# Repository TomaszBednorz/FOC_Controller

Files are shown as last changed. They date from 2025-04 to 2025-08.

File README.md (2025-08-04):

# FOC_Controller - in progress

## Description

The main goal of this project is to design a driver for a PMSM (Permanent Magnet Synchronous Motor) and implement the FOC (Field-Oriented Control) algorithm in software - in the future.

## Hardware overview



More information: [Hardware folder](https://github.com/TomaszBednorz/FOC_Controller/tree/main/HW)

## Figres

The FOC controller and PMSM motor.  



## STM32CubeIDE template


Empty project with pins and peripherals configuration: [Template](https://github.com/TomaszBednorz/FOC_Controller/tree/main/Tools/STM32CubeIDE_projects/STM32G473RC_template)

## Software overview

TBD

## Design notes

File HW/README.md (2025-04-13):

# FOC_Controller – Hardware

## Description

This folder contains:
- Source files of the PCB design in KiCad: [PCB folder](https://github.com/TomaszBednorz/FOC_Controller/tree/main/HW/PCB)
- STL files for the motor driver enclosure.

## 3D Visualization




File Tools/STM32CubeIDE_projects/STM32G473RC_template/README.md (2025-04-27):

# Configuration overview

## Description

This folder contains an empty project in STM32CubeIDE with the MCU configuration required for further software development. It serves as a project base.



### Clock Configuration
- HSE Value: 24 MHz (Quartz crystal frequency)
- System Clock Frequency: 160 MHz (AHB, APB1, APB2)
- Pins: PF0 [RCC_OSC_IN], PF1: [RCC_OSC_OUT]

### ADC
TODO

### CAN FD
- Baud Rate (Nominal): 1 Mbps
- Baud Rate (Data): 5 Mbps
- Pins: PA11 [CANFD_RX], PA12[CANFD_TX]
  
### SPI - TMAG5170 Hall sensor
- Calculated Baud Rate: 10 Mbps
- SPI mode: 0 (CPOL=0, CPHA=0)
- Data Size: 8-bit
- Direction: 2-line (Full Duplex)
- Pins: PA4 [HALL_SPI_CS], PA5 [HALL_SPI_SCK], PA6: [HALL_SPI_MISO], PA7 [HALL_SPI_MOSI]
  
### UART - Debug
- Baud Rate: 460800 bps
- Pins: PB6 [UART_TX], PB7 [UART_RX]

### Timer - PWM
TODO

### Serial wire debug
- Pins: PA13: [SWD_SWDIO], PA14 [SWD_SWCLK]

### Other GPIO - TODO

// ADC
- PA0: BEMF_C (ADC1_IN1)
- PA1: BEMF_B (ADC1_IN2)
- PA2: BEMF_A (ADC1_IN3)
- PC1: MOTOR_DRV_SOC (ADC1_IN7)
- PC2: MOTOR_DRV_SOB (ADC1_IN8)
- PC3: MOTOR_DRV_SOA (ADC1_IN9)
- PB11: VBAT_SENSE (ADC1_IN14)

// PWM
- PA8: MOTOR_DRV_INHA (TIM1_CH1)
- PA9: MOTOR_DRV_INHB (TIM1_CH2)
- PA10: MOTOR_DRV_INHC (TIM1_CH3)
- PB13: MOTOR_DRV_INLA (TIM1_CH1N)
- PB14: MOTOR_DRV_INLB (TIM1_CH2N)
- PB15: MOTOR_DRV_INLC (TIM1_CH3N)

// GPIO
- PB0: USER_LED - TODO
- PB1: USER_BUTTON - TODO
- PB8: BOOT - TODO
- PC4: HALL_ALERT - Hall sensor interrupt
- PC7: MOTOR_DRV_NFAULT - TODO
- PC8: MOTOR_DRV_NSLEEP - TODO
- PC11: CAN_TRCV_STB - TODO
- PC13: DEBUG_PIN_RED - TODO
- PC15: DEBUG_PIN_BLUE - TODO
- PG10: NRST - TODO

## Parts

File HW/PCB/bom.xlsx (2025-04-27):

Component | Name | Price [zl] | Quantity | Sum | Status | Code case | Link | Designator
Integrated circuits
MCU | STM32G473RCT6 | 20.94 | 2 | 41.88 | Mouser |  | https://www.mouser.pl/ProductDetail/STMicroelectronics/STM32G473RCT6?qs=uwxL4vQweFM8hYulqmXtPg%3D%3D | U2
Motor driver | DRV8317HREER | 9.29 | 2 | 18.58 | Mouser |  | https://www.mouser.pl/ProductDetail/Texas-Instruments/DRV8317HREER?qs=amGC7iS6iy%252BMUwpQq07OLg%3D%3D | U3
CAN-FD transceiver | TCAN3414DR | 5.81 | 2 | 11.62 | Mouser |  | https://www.mouser.pl/ProductDetail/Texas-Instruments/TCAN3413DR?qs=mELouGlnn3eIMT2B6sccyw%3D%3D | U5
Hall sensor | TMAG5170A2QDGKR | 7.1 | 2 | 14.2 | Mouser |  | https://www.mouser.pl/ProductDetail/Texas-Instruments/TMAG5170A2QDGKR?qs=XAiT9M5g4x%2Fpn0mMRKz0SA%3D%3D | U4
Step-down converter | TPS54228D | 4.69 | 2 | 9.38 | Mouser |  | https://www.mouser.pl/ProductDetail/Texas-Instruments/TPS54228D?qs=gXEV9p%2FxLgfhSBr1zrUV%2FQ%3D%3D | U1
Resistors
33k | CRCW080533K0FKEBC | 0.065 | 15 | 0.975 | Mouser | 0805 | https://www.mouser.pl/ProductDetail/Vishay-Dale/CRCW080533K0FKEBC | R1, R5, R21, R23, R25
10k | CRCW080510K0FKEA | 0.172 | 21 | 3.612 | Mouser | 0805 | https://www.mouser.pl/ProductDetail/Vishay-Dale/CRCW080510K0FKEA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 | R2, R4, R7, R10, R22, R24, R26
110k | CRCW0805110KFKEAC | 0.099 | 10 | 0.99 | Mouser | 0805 | https://www.mouser.pl/ProductDetail/Vishay-Dale/CRCW0805110KFKEAC | R3
1k | CRCW08051K00FKEAC | 0.099 | 10 | 0.99 | Mouser | 0805 | https://www.mouser.pl/ProductDetail/Vishay-Dale/CRCW08051K00FKEAC | R6,R8
0R | AC0805FR-070RL | 0.065 | 10 | 0.65 | Mouser | 0805 | https://www.mouser.pl/ProductDetail/YAGEO/AC0805FR-070RL?qs=sGAEpiMZZMvdGkrng054twVr7TWeaA0stZVp9zaHJmE%3D | R9 (brak), R16, R17, R19
5k1 | CRCW08055K10FKEAC | 0.099 | 10 | 0.99 | Mouser | 0805 | https://www.mouser.pl/ProductDetail/Vishay-Dale/CRCW08055K10FKEAC | R11
330R | CRCW0805330RFKEA | 0.103 | 10 | 1.03 | Mouser | 0805 | https://www.mouser.pl/ProductDetail/Vishay-Dale/CRCW0805330RFKEA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 | R12, R13, R14 | -
4k7 | CRCW08054K70FKEA | 0.12 | 10 | 1.2 | Mouser | 0805 | https://www.mouser.pl/ProductDetail/Vishay-Dale/CRCW08054K70FKEA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 | R27
120R | CRCW0805120RFKEA | 0.159 | 10 | 1.59 | Mouser | 0805 | https://www.mouser.pl/ProductDetail/Vishay-Dale/CRCW0805120RFKEA | R28
NC |  |  | 9 | 0 |  |  |  | R15, R19, R20
Capacitors
100u/25V, electrolytic | 860010473007 | 0.53 | 2 | 1.06 | Mouser | THT | https://www.mouser.pl/ProductDetail/Wurth-Elektronik/860010473007 | C1
10u/25V | CL21A106KAYNNNG | 0.301 | 10 | 3.01 | Mouser | 0805 | https://www.mouser.pl/ProductDetail/Samsung-Electro-Mechanics/CL21A106KAYNNNG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 | C2, C3, C11
100n/50V | CL21B104KBCNNND | 0.077 | 100 | 7.7 | Mouser | 0805 | https://www.mouser.pl/ProductDetail/Samsung-Electro-Mechanics/CL21B104KBCNNND?qs=349EhDEZ59q4Uk9cKG1Kkg%3D%3D | C4, C7, C10, C12, C13, C14, C15, C16, C17, C20, C23, C25, C26, C30, C31, C32, C39, C41, C42
1u/50V | CL21B105KBFNNNE | 0.151 | 15 | 2.265 | Mouser | 0805 | https://www.mouser.pl/ProductDetail/Samsung-Electro-Mechanics/CL21B105KBFNNNE?qs=yOVawPpwOwmddQEBPU6Y9A%3D%3D | C5, C18, C19, C24, C40
3n3/25V | 885012207063 | 0.155 | 10 | 1.55 | Mouser | 0805 | https://www.mouser.pl/ProductDetail/Wurth-Elektronik/885012207063?qs=0KOYDY2FL29qg3SFvr%2F81Q%3D%3D | C6
22u/25V | CL21A226MAYNNNE | 0.426 | 15 | 6.39 | Mouser | 0805 | https://www.mouser.pl/ProductDetail/Samsung-Electro-Mechanics/CL21A226MAYNNNE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 | C8, C9, [C27, C28, C29]->22p
27p/50V | CL10C270JB81PNC | 0.116 | 10 | 1.16 | Mouser | 0603 | https://www.mouser.pl/ProductDetail/Samsung-Electro-Mechanics/CL10C270JB81PNC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 | C21, C22
10u/25V, electrolytic | 865080440002 | 0.74 | 4 | 2.96 | Mouser | SMD | https://www.mouser.pl/ProductDetail/Wurth-Elektronik/865080440002 | C33, C35
2u2/25V | CL21A225KAFNNNG | 0.219 | 10 | 2.19 | Mouser | 0805 | https://www.mouser.pl/ProductDetail/Samsung-Electro-Mechanics/CL21A225KAFNNNG?qs=yOVawPpwOwlfuACaawXMWQ%3D%3D | C34
1n6/50V | GRM1885C1H162JA01D | 0.129 | 10 | 1.29 | TME | 0603 | https://www.tme.eu/pl/details/grm1885c1h162ja01d/kondensatory-mlcc-smd/murata/ | C36, C37, C38
47p | CL10C470JC81PNC | 0.163 | 10 | 1.63 | Mouser | 0603 | https://www.mouser.pl/ProductDetail/Samsung-Electro-Mechanics/CL10C470JC81PNC?qs=zijbFIqa2JHu3PDRMJ4hNA%3D%3D | C43, C44
Inductors
3u3 | NRS4012T3R3MDGJ | 0.78 | 3 | 2.34 | Mouser |  | https://www.mouser.pl/ProductDetail/TAIYO-YUDEN/NRS4012T3R3MDGJ?qs=PzICbMaShUd7bwjzDBeuGQ%3D%3D | L1
Diodes
Schottky Diodes | SK22 | 0.74 | 3 | 2.22 | Mouser |  | https://www.mouser.pl/ProductDetail/Diotec-Semiconductor/SK22?qs=OlC7AqGiEDnotPkeKaADTg%3D%3D | D1
LED green | 150080GS75000 | 0.78 | 3 | 2.34 | Mouser |  | https://www.mouser.pl/ProductDetail/Wurth-Elektronik/150080GS75000 | D2
LED blue | 150080BS75000 | 0.78 | 3 | 2.34 | Mouser |  | https://www.mouser.pl/ProductDetail/Wurth-Elektronik/150080BS75000 | D3
Ferrite Beads
600R/100Mhz | MPZ2012S601ATD25 | 0.28 | 10 | 2.8 | Mouser | 0805 | https://www.mouser.pl/ProductDetail/TDK/MPZ2012S601ATD25?qs=n0%2F4YYxsltT7vo9AjVUU7w%3D%3D | FB1
Cristals
24MHz | ABM3-24.000MHZ-D2Y-T | 2.21 | 2 | 4.42 | Mouser |  | https://www.mouser.pl/ProductDetail/ABRACON/ABM3-24.000MHZ-D2Y-T?qs=ihRgKfnEsN7QIYosfWUeVg%3D%3D | X1
Switches
Tactile Switch | TS04-66-55-BK-100-SMT | 0.66 | 4 | 2.64 | Mouser |  | https://www.mouser.pl/ProductDetail/Same-Sky/TS04-66-55-BK-100-SMT | SW1, SW2
Connectors
DC male connector | XT30PW-M | 2.54 | 2 | 5.08 | TME |  | https://www.tme.eu/pl/details/xt30pw-m/zlacza-dc/amass/ | J1
DC female connector | XT30U-F | 1.75 | 2 | 3.5 | TME |  | https://www.tme.eu/pl/details/xt30u-f/zlacza-dc/amass/ | J1
Header 1x10 (goldpin) | 10129378-910001BLF | 0.78 | 2 | 1.56 | Mouser |  | https://www.mouser.pl/ProductDetail/Amphenol-FCI/10129378-910001BLF?qs=0lQeLiL1qyaKTim8PTf2WA%3D%3D | J2, J4
Header 2x5 | 20021121-00010T4LF | 3.23 | 2 | 6.46 | Mouser |  | https://www.mouser.pl/ProductDetail/Amphenol-FCI/20021121-00010T4LF?qs=oJs1R%252BxK6kTva5Su0CuB6g%3D%3D | J3
Screw terminal 1x3 | EBWA-03-A | 1.76 | 2 | 3.52 | Mouser |  | https://www.mouser.pl/ProductDetail/Adam-Tech/EBWA-03-A?qs=HoCaDK9Nz5eL6P8%252BJvt%2FAA%3D%3D | J6
Jumper 1x2 | MSA-G | 0.41 | 3 | 1.23 | Mouser |  | https://www.mouser.pl/ProductDetail/Adam-Tech/MSA-G?qs=TTVbHWoAP%2FQyJO4lrxmkwg%3D%3D | J5
 |  |  | Łącznie | 179.342

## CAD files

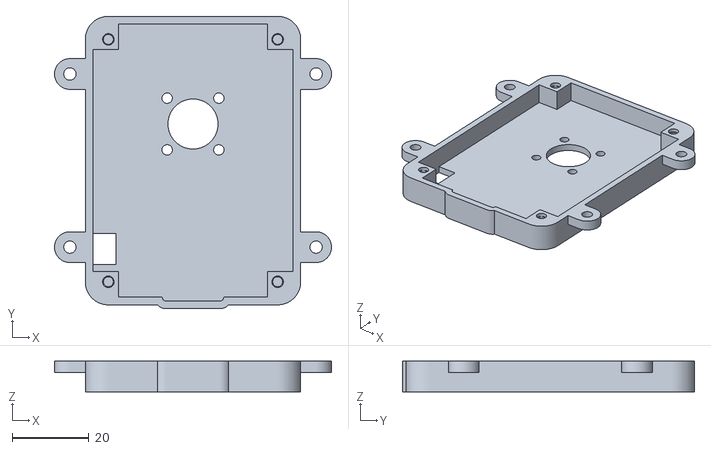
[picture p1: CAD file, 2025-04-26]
HW/Enclosure/Base.stl
72.0 x 76.0 x 8.00

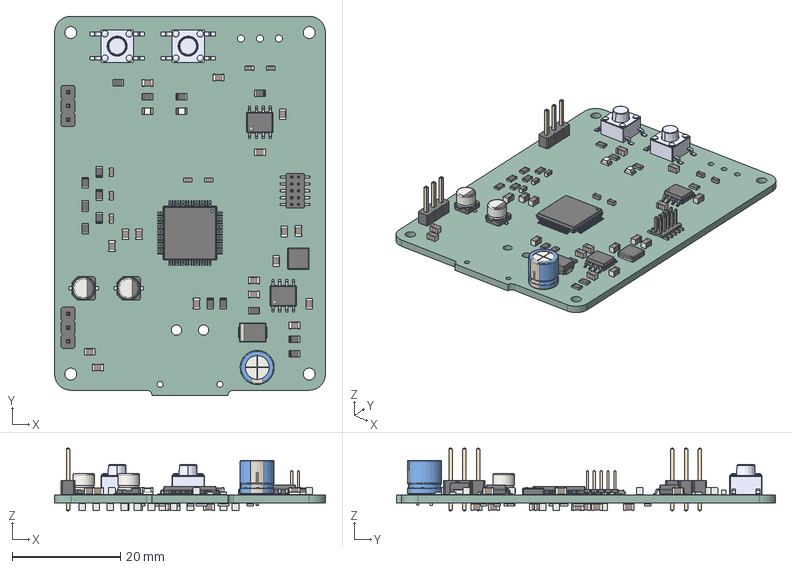
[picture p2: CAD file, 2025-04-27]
HW/PCB/FOC_Controller.step
50.0 x 70.0 x 11.5 mm
C_0805_2012Metric x 34
SOIC-8_3.9x4.9mm_P1.27mm x 2
R_0805_2012Metric x 27
CP_Elec_4x3.9 x 2
C_0603_1608Metric x 7
LQFP-64_10x10mm_P0.5mm
D_SMB
TS04-66-55-BK-100-SMT-TR x 2
L_0805_2012Metric
CP_Radial_D6.3mm_P2.50mm
LED_0805_2012Metric x 2
PinHeader_2x05_P1.27mm_Vertical_SMD
PinHeader_1x03_P2.54mm_Vertical x 2
L_APV_ANR4012
FOC_Controller_PCB

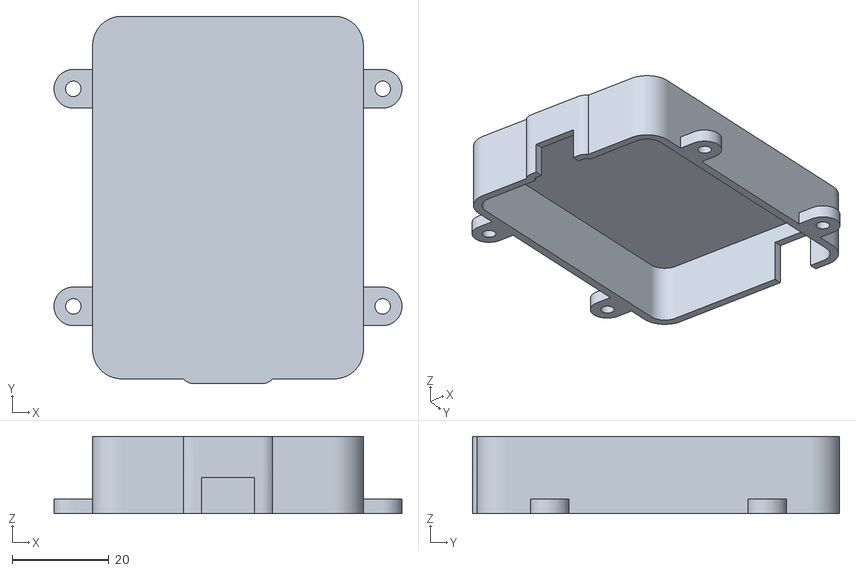
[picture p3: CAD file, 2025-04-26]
HW/Enclosure/Lid.stl
72.0 x 76.0 x 16.0

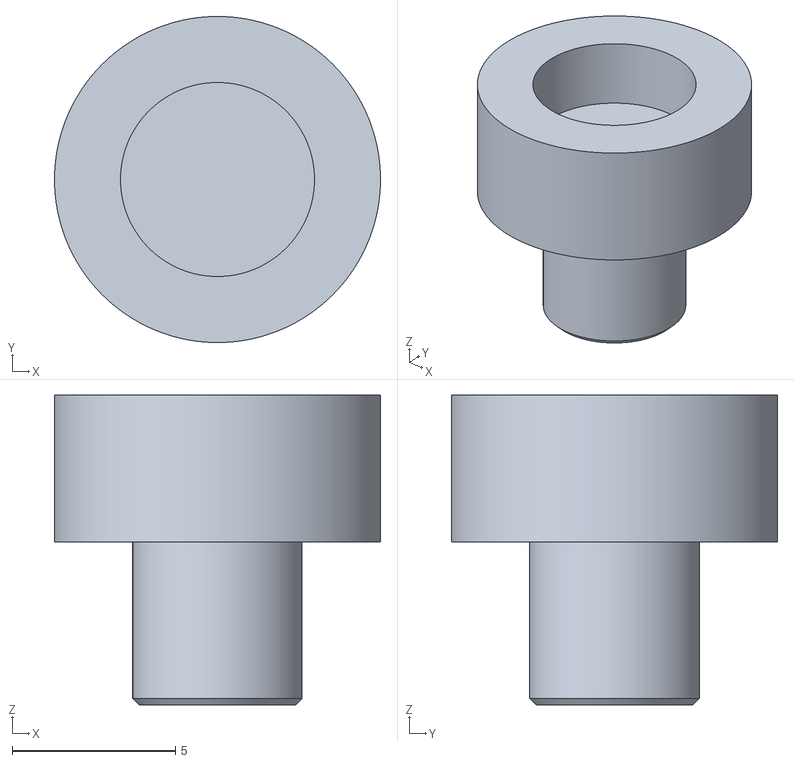
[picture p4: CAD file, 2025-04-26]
HW/Enclosure/Magnet_holder.stl
10.0 x 10.00 x 9.50

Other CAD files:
HW/Enclosure/Lid_for_development.stl

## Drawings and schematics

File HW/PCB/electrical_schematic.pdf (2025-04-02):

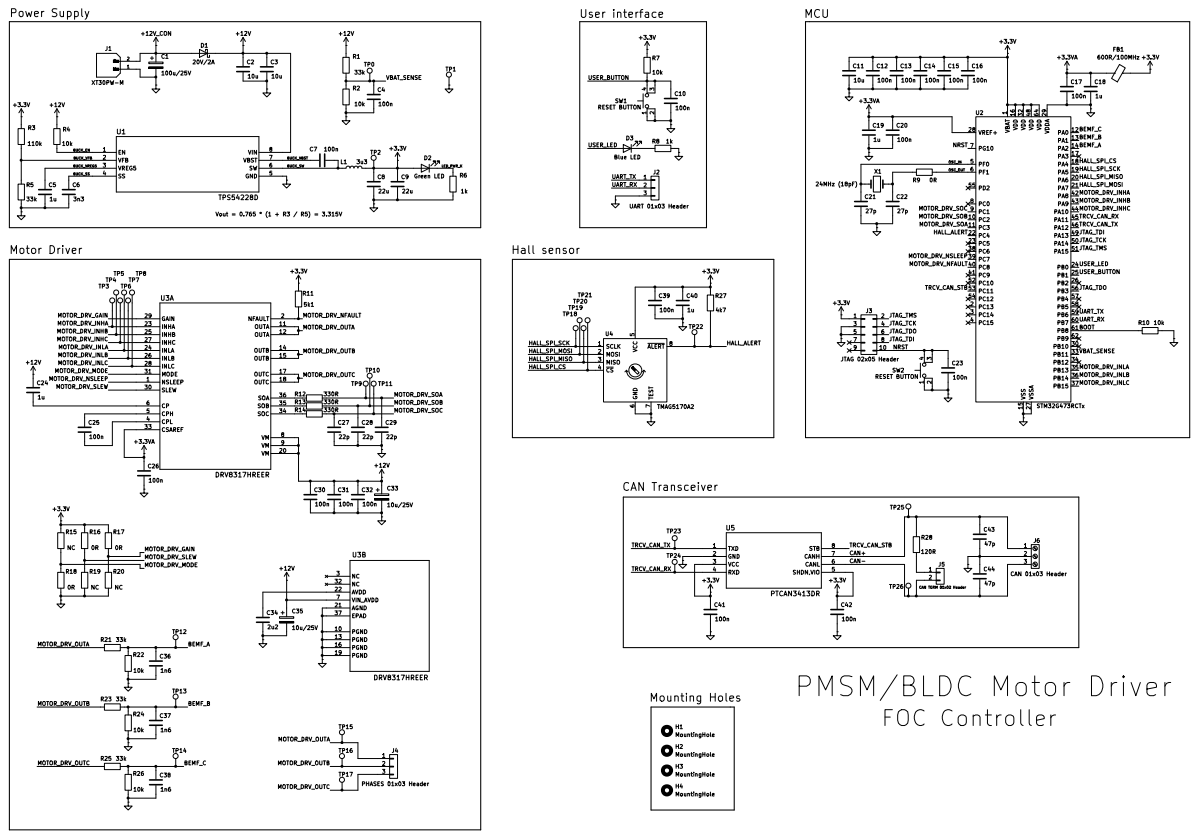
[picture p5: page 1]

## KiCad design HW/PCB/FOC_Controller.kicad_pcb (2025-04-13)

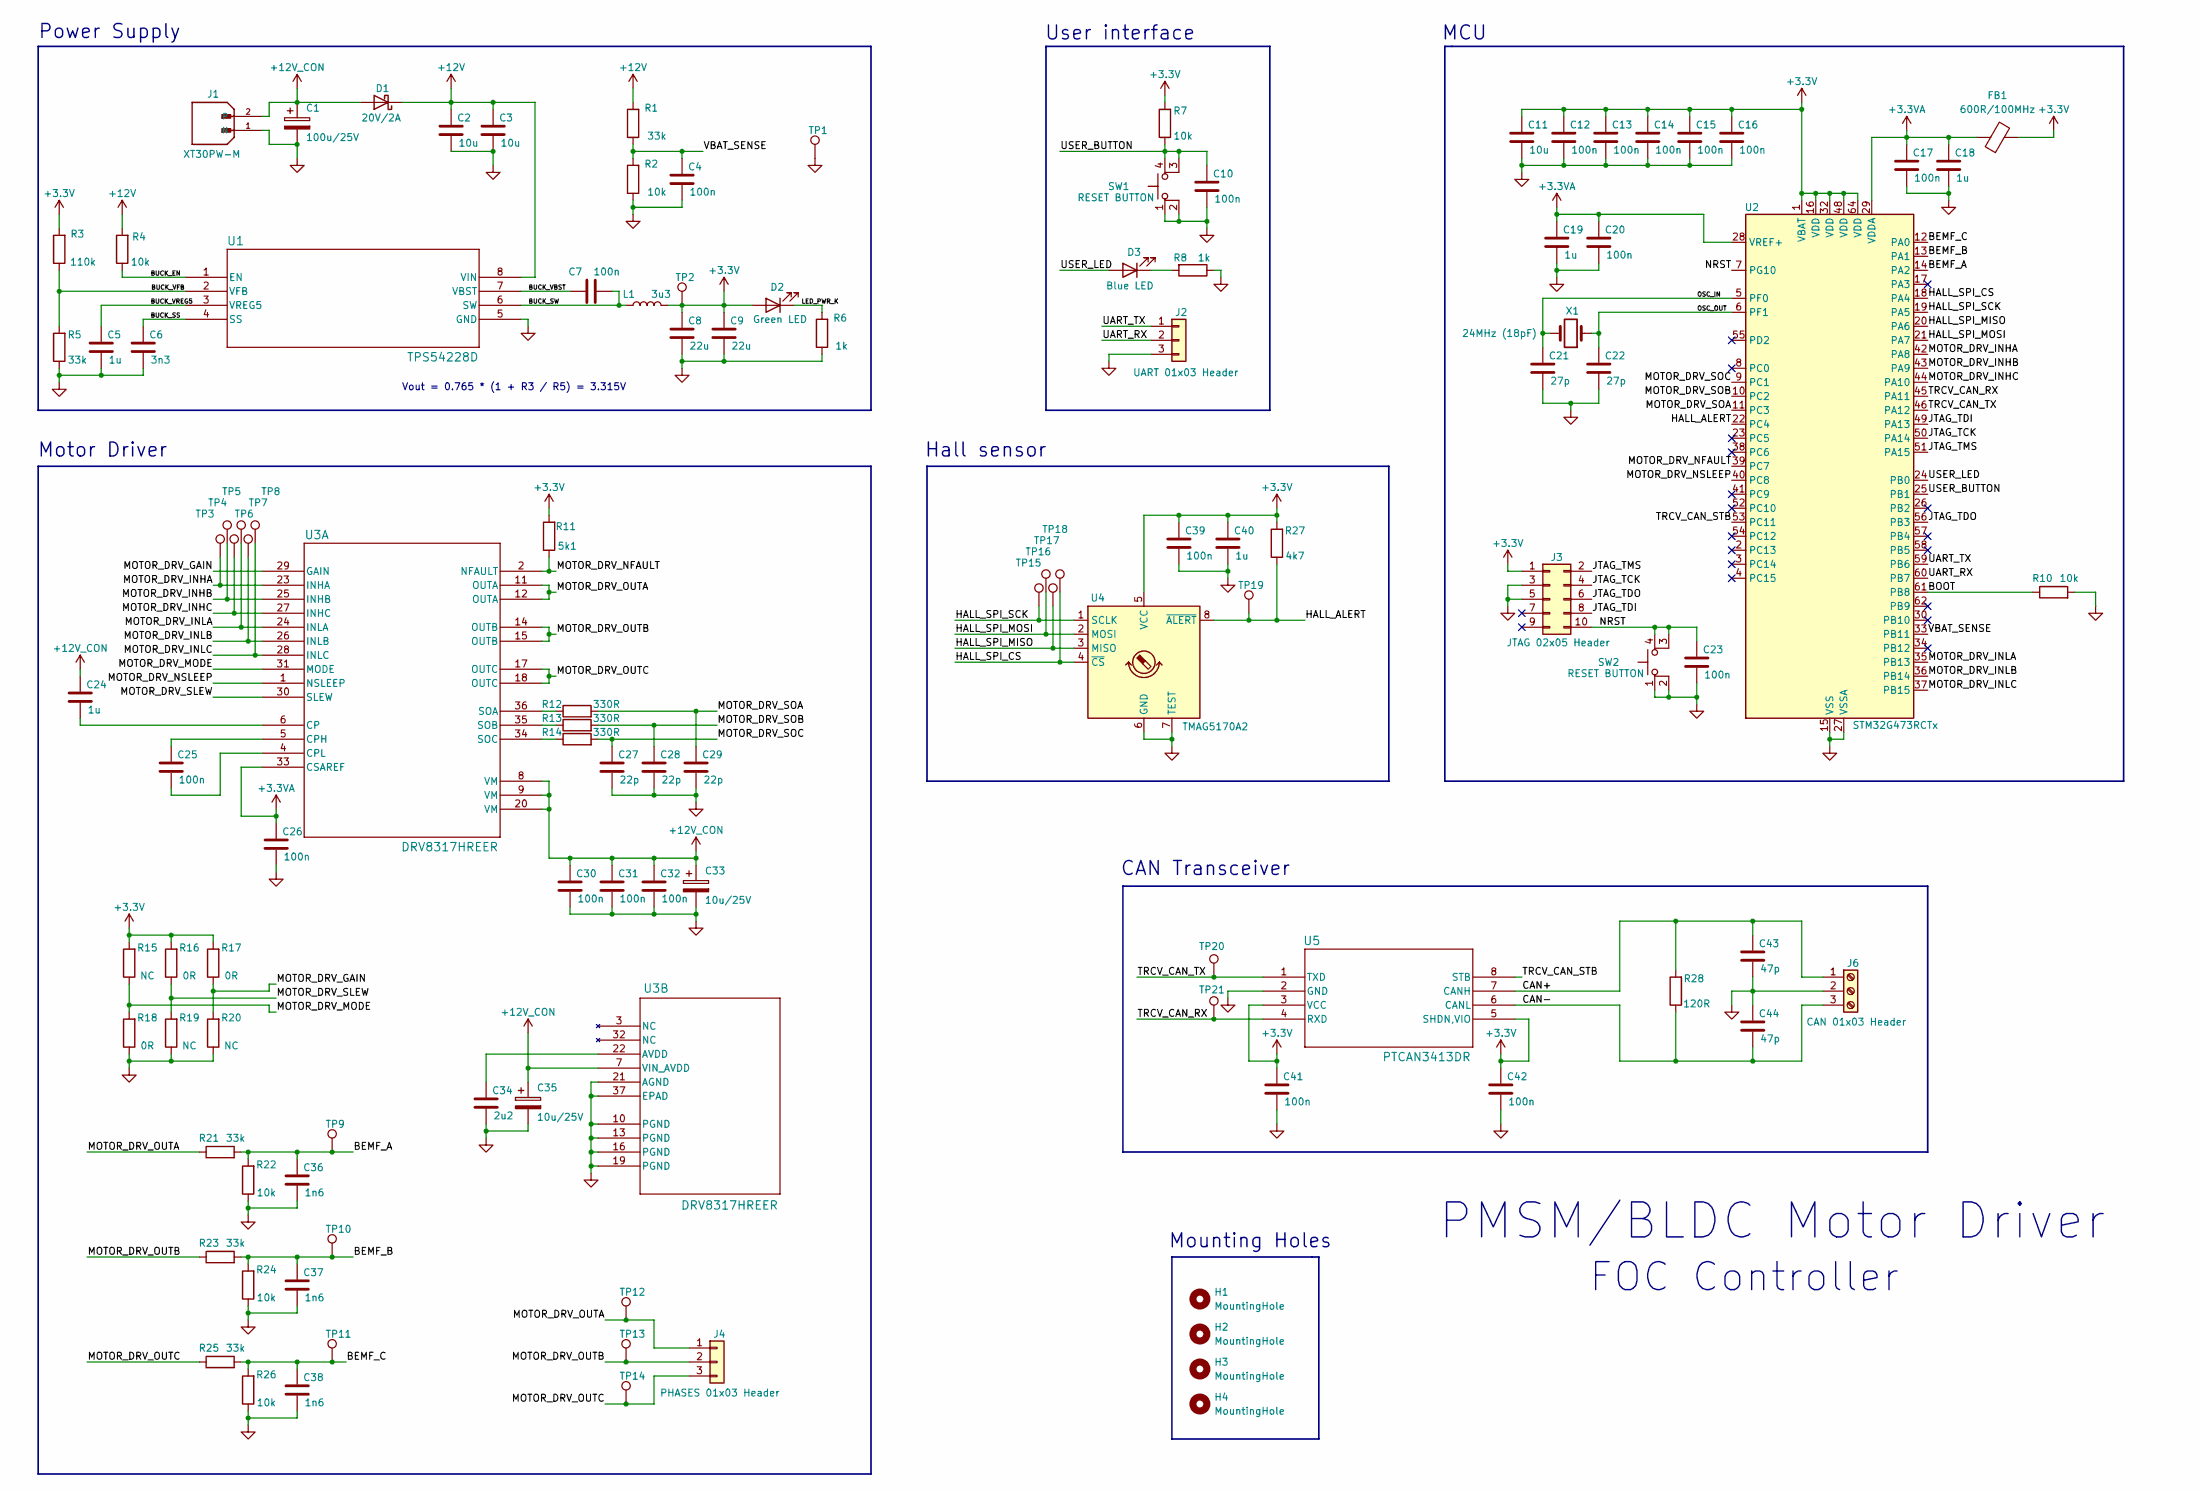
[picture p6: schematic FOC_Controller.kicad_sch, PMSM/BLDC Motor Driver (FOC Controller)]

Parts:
C1: 100u/25V; CP_Radial_D6.3mm_P2.50mm
C2, C3, C11: 10u; C_0805_2012Metric_Pad1.18x1.45mm_HandSolder
C4, C7, C10, C12, C13, C14, C15, C16, C17, C20, C23, C25, C26, C30, C31, C32, C39, C41, C42: 100n; C_0805_2012Metric_Pad1.18x1.45mm_HandSolder
C5, C18, C19, C24, C40: 1u; C_0805_2012Metric_Pad1.18x1.45mm_HandSolder
C6: 3n3; C_0805_2012Metric_Pad1.18x1.45mm_HandSolder
C8, C9: 22u; C_0805_2012Metric_Pad1.18x1.45mm_HandSolder
C21, C22: 27p; C_0603_1608Metric_Pad1.08x0.95mm_HandSolder
C27, C28, C29: 22p; C_0805_2012Metric_Pad1.18x1.45mm_HandSolder
C33, C35: 10u/25V; CP_Elec_4x3.9
C34: 2u2; C_0805_2012Metric_Pad1.18x1.45mm_HandSolder
C36, C37, C38: 1n6; C_0603_1608Metric_Pad1.08x0.95mm_HandSolder
C43, C44: 47p; C_0603_1608Metric_Pad1.08x0.95mm_HandSolder
D1: 20V/2A; D_SMB
D2: Green LED; LED_0805_2012Metric_Pad1.15x1.40mm_HandSolder
D3: Blue LED; LED_0805_2012Metric_Pad1.15x1.40mm_HandSolder
FB1: 600R/100MHz; L_0805_2012Metric_Pad1.05x1.20mm_HandSolder
H1, H2, H3, H4: MountingHole; MountingHole_2.2mm_M2
J1: XT30PW-M; AMASS_XT30PW-M_1x02_P2.50mm_Horizontal; PARTREV 1.2
J2: UART 01x03 Header; PinHeader_1x03_P2.54mm_Vertical
J3: JTAG 02x05 Header; PinHeader_2x05_P1.27mm_Vertical_SMD
J4: PHASES 01x03 Header; PinHeader_1x03_P2.54mm_Vertical
J6: CAN 01x03 Header; TerminalBlock_MetzConnect_Type059_RT06303HBWC_1x03_P3.50mm_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
L1: 3u3; L_APV_ANR4012
R1, R5, R21, R23, R25: 33k; R_0805_2012Metric_Pad1.20x1.40mm_HandSolder
R2, R4, R7, R10, R22, R24, R26: 10k; R_0805_2012Metric_Pad1.20x1.40mm_HandSolder
R3: 110k; R_0805_2012Metric_Pad1.20x1.40mm_HandSolder
R6, R8: 1k; R_0805_2012Metric_Pad1.20x1.40mm_HandSolder
R11: 5k1; R_0805_2012Metric_Pad1.20x1.40mm_HandSolder
R12, R13, R14: 330R; R_0805_2012Metric_Pad1.20x1.40mm_HandSolder
R15, R19, R20: NC; R_0805_2012Metric_Pad1.20x1.40mm_HandSolder
R16, R17, R18: 0R; R_0805_2012Metric_Pad1.20x1.40mm_HandSolder
R27: 4k7; R_0805_2012Metric_Pad1.20x1.40mm_HandSolder
R28: 120R; R_0805_2012Metric_Pad1.20x1.40mm_HandSolder
SW1, SW2: RESET BUTTON; SW_TS04-66-55-BK-100-SMT-TR
TP1, TP2, TP3, TP4, TP5, TP6, TP7, TP8, TP9, TP10, TP11, TP12, TP13, TP14, TP15, TP16, TP17, TP18, TP19, TP20, TP21: TestPoint; TestPoint_Pad_D1.0mm
U1: TPS54228D; SOIC-8_3.9x4.9mm_P1.27mm
U2: STM32G473RCTx; LQFP-64_10x10mm_P0.5mm
U3: DRV8317HREER; WQFN36_REE_TEX-L
U4: TMAG5170A2; VSSOP-8_3x3mm_P0.65mm
U5: PTCAN3413DR; SOIC-8_3.9x4.9mm_P1.27mm
X1: 24MHz (18pF); Crystal_SMD_Abracon_ABM3-2Pin_5.0x3.2mm_HandSoldering

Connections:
+3.3V: C8.1, C9.1, C11.1, C12.1, C13.1, C14.1, C15.1, C16.1, C39.1, C40.1, C41.1, C42.1, D2.2 (A), FB1.2, J3.1, L1.2, R3.2, R7.2, R11.2, R15.2, R16.2, R17.2, R27.2, TP2.1, U2.1 (VBAT), U2.16 (VDD), U2.32 (VDD), U2.48 (VDD), U2.64 (VDD), U4.5 (VCC), U5.3 (VCC), U5.5 (SHDN,VIO)
+3.3VA: C17.1, C18.1, C19.1, C20.1, C26.1, FB1.1, U2.28 (VREF+), U2.29 (VDDA), U3.33 (CSAREF)
+12V: C2.1, C3.1, D1.1 (K), R1.2, R4.2, U1.8 (VIN)
+12V_CON: C1.1, C24.1, C30.1, C31.1, C32.1, C33.1, C35.1, D1.2 (A), J1.2, U3.7 (VIN_AVDD), U3.8 (VM), U3.9 (VM), U3.20 (VM)
/BEMF_A: C36.1, R21.2, R22.2, TP9.1, U2.14 (PA2)
/BEMF_B: C37.1, R23.2, R24.2, TP10.1, U2.13 (PA1)
/BEMF_C: C38.1, R25.2, R26.2, TP11.1, U2.12 (PA0)
/BOOT: R10.1, U2.61 (PB8)
/BUCK_EN: R4.1, U1.1 (EN)
/BUCK_SS: C6.1, U1.4 (SS)
/BUCK_SW: C7.2, L1.1, U1.6 (SW)
/BUCK_VBST: C7.1, U1.7 (VBST)
/BUCK_VFB: R3.1, R5.2, U1.2 (VFB)
/BUCK_VREG5: C5.1, U1.3 (VREG5)
/CAN+: C43.1, J6.1, R28.2, U5.7 (CANH)
/CAN-: C44.2, J6.3, R28.1, U5.6 (CANL)
/HALL_ALERT: R27.1, TP19.1, U2.22 (PC4), U4.8 (~ALERT)
/HALL_SPI_CS: TP18.1, U2.18 (PA4), U4.4 (~CS)
/HALL_SPI_MISO: TP17.1, U2.20 (PA6), U4.3 (MISO)
/HALL_SPI_MOSI: TP16.1, U2.21 (PA7), U4.2 (MOSI)
/HALL_SPI_SCK: TP15.1, U2.19 (PA5), U4.1 (SCLK)
/JTAG_TCK: J3.4, U2.50 (PA14)
/JTAG_TDI: J3.8, U2.49 (PA13)
/JTAG_TDO: J3.6, U2.56 (PB3)
/JTAG_TMS: J3.2, U2.51 (PA15)
/LED_PWR_K: D2.1 (K), R6.2
/MOTOR_DRV_GAIN: R17.1, R20.2, U3.29 (GAIN)
/MOTOR_DRV_INHA: TP3.1, U2.42 (PA8), U3.23 (INHA)
/MOTOR_DRV_INHB: TP4.1, U2.43 (PA9), U3.25 (INHB)
/MOTOR_DRV_INHC: TP5.1, U2.44 (PA10), U3.27 (INHC)
/MOTOR_DRV_INLA: TP6.1, U2.35 (PB13), U3.24 (INLA)
/MOTOR_DRV_INLB: TP7.1, U2.36 (PB14), U3.26 (INLB)
/MOTOR_DRV_INLC: TP8.1, U2.37 (PB15), U3.28 (INLC)
/MOTOR_DRV_MODE: R15.1, R18.2, U3.31 (MODE)
/MOTOR_DRV_NFAULT: R11.1, U2.39 (PC7), U3.2 (NFAULT)
/MOTOR_DRV_NSLEEP: U2.40 (PC8), U3.1 (NSLEEP)
/MOTOR_DRV_OUTA: J4.1, R21.1, TP12.1, U3.11 (OUTA), U3.12 (OUTA)
/MOTOR_DRV_OUTB: J4.2, R23.1, TP13.1, U3.14 (OUTB), U3.15 (OUTB)
/MOTOR_DRV_OUTC: J4.3, R25.1, TP14.1, U3.17 (OUTC), U3.18 (OUTC)
/MOTOR_DRV_SLEW: R16.1, R19.2, U3.30 (SLEW)
/MOTOR_DRV_SOA: C29.1, R12.2, U2.11 (PC3)
/MOTOR_DRV_SOB: C28.1, R13.2, U2.10 (PC2)
/MOTOR_DRV_SOC: C27.1, R14.2, U2.9 (PC1)
/NRST: C23.1, J3.10, SW2.3 (K), SW2.4 (A), U2.7 (PG10)
/OSC_IN: C21.1, U2.5 (PF0), X1.2
/OSC_OUT: C22.1, U2.6 (PF1), X1.1
/TRCV_CAN_RX: TP21.1, U2.45 (PA11), U5.4 (RXD)
/TRCV_CAN_STB: U2.53 (PC11), U5.8 (STB)
/TRCV_CAN_TX: TP20.1, U2.46 (PA12), U5.1 (TXD)
/UART_RX: J2.2, U2.60 (PB7)
/UART_TX: J2.1, U2.59 (PB6)
/USER_BUTTON: C10.1, R7.1, SW1.3 (K), SW1.4 (A), U2.25 (PB1)
/USER_LED: D3.2 (A), U2.24 (PB0)
/VBAT_SENSE: C4.1, R1.1, R2.2, U2.33 (PB11)
GND: C1.2, C2.2, C3.2, C4.2, C5.2, C6.2, C8.2, C9.2, C10.2, C11.2, C12.2, C13.2, C14.2, C15.2, C16.2, C17.2, C18.2, C19.2, C20.2, C21.2, C22.2, C23.2, C26.2, C27.2, C28.2, C29.2, C30.2, C31.2, C32.2, C33.2, C34.2, C35.2, C36.2, C37.2, C38.2, C39.2, C40.2, C41.2, C42.2, C43.2, C44.1, J1.1 (N), J2.3, J3.3, J3.5, J6.2, R2.1, R5.1, R6.1, R8.1, R10.2, R18.1, R19.1, R20.1, R22.1, R24.1, R26.1, SW1.1, SW1.2, SW2.1, SW2.2, TP1.1, U1.5 (GND), U2.15 (VSS), U2.27 (VSSA), U2.31 (VSS), U2.47 (VSS), U2.63 (VSS), U3.10 (PGND), U3.13 (PGND), U3.16 (PGND), U3.19 (PGND), U3.21 (AGND), U3.37 (EPAD), U4.6 (GND), U4.7 (TEST), U5.2 (GND)
unnamed: D3.1 (K), R8.2
unnamed: C24.2, U3.6 (CP)
unnamed: C25.1, U3.5 (CPH)
unnamed: C25.2, U3.4 (CPL)
unnamed: R12.1, U3.36 (SOA)
unnamed: R13.1, U3.35 (SOB)
unnamed: R14.1, U3.34 (SOC)
unnamed: C34.1, U3.22 (AVDD)

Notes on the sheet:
Power Supply
User interface
Mounting Holes
Hall sensor
CAN Transceiver
MCU
Motor Driver
Vout = 0.765 * (1 + R3 / R5) = 3.315V
PMSM/BLDC Motor Driver
FOC Controller

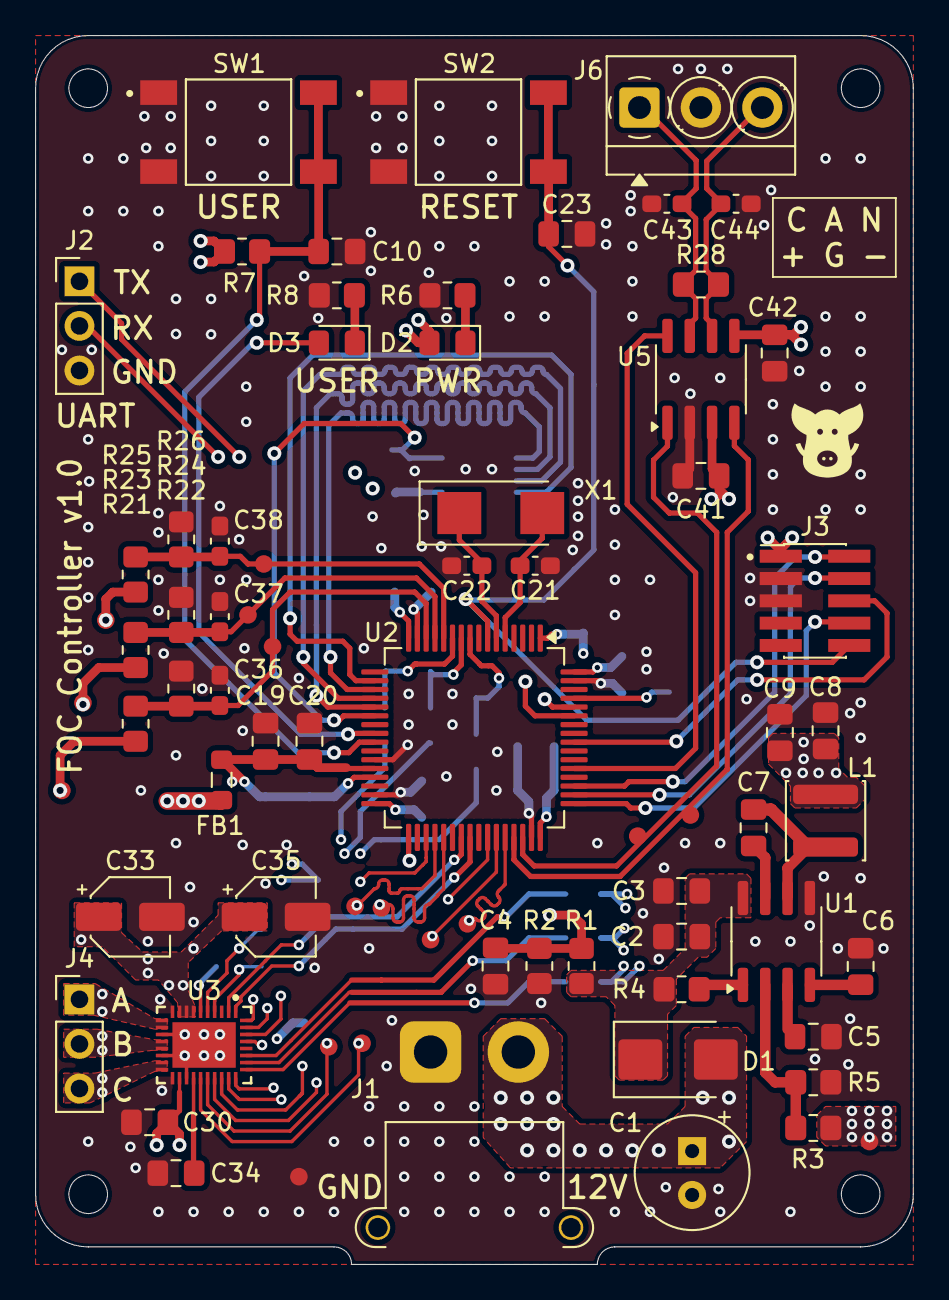
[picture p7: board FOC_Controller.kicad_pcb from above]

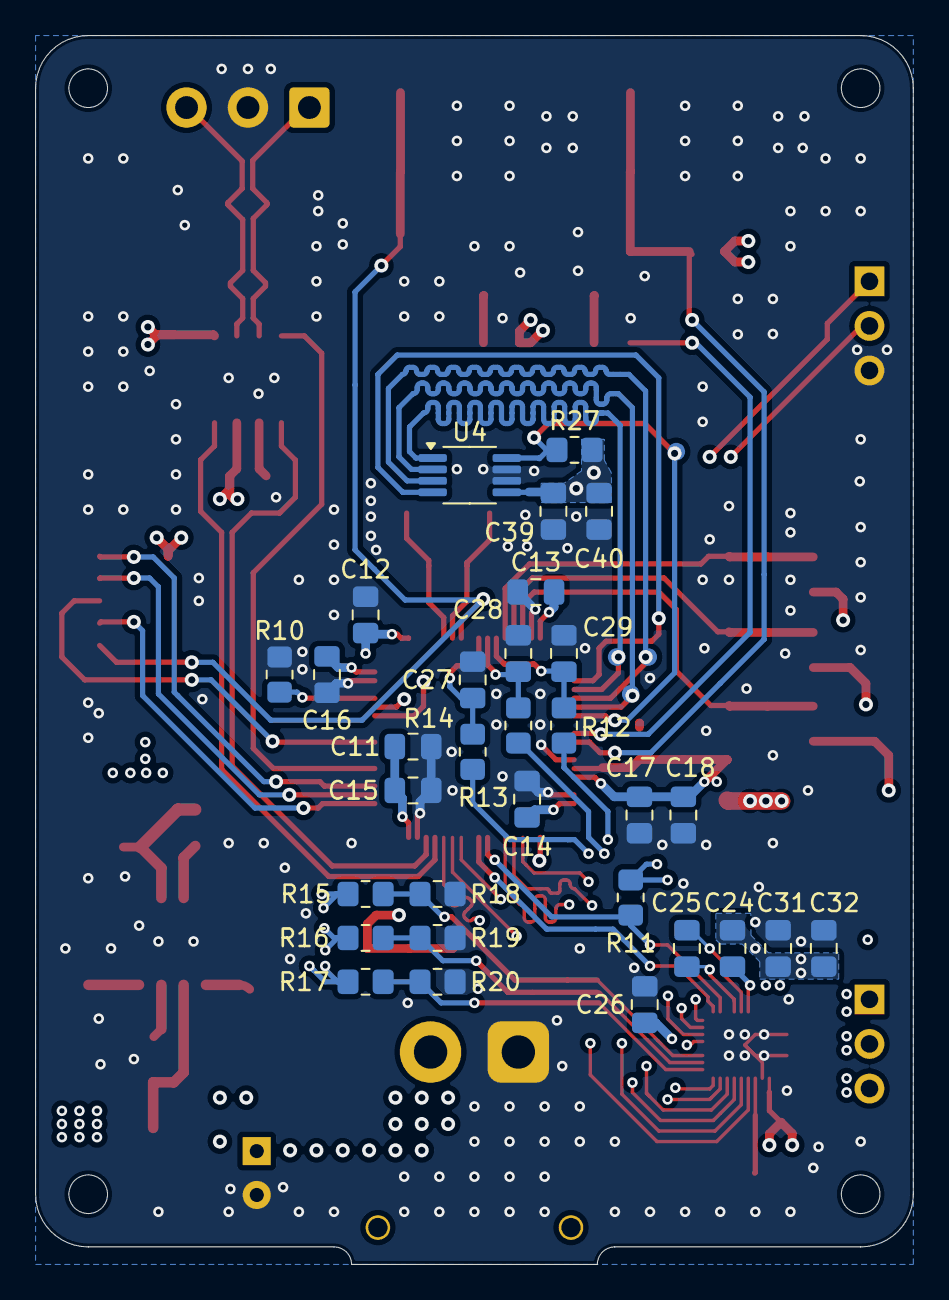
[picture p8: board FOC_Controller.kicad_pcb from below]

Board: 4 copper layers, 50.0 x 70.0 mm, 114 parts (36 on the bottom side), 63 nets.

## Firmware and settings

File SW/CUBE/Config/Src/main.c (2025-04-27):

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
/* Includes ------------------------------------------------------------------*/
#include "main.h"
#include "adc.h"
#include "cordic.h"
#include "fdcan.h"
#include "spi.h"
#include "tim.h"
#include "usart.h"
#include "gpio.h"

/* USER CODE BEGIN Includes */
#include <stdio.h>
/* USER CODE END Includes */


void SystemClock_Config(void);
/* USER CODE BEGIN 0 */
float ConvertRawToMilliTesla(int16_t raw_value)
{
    // Zakładamy, że pełna skala to 300 mT przy maksymalnej wartości
    return ((float)raw_value) * 75.0f / 32768.0f;
}
/* USER CODE END 0 */

/**
  * @brief  The application entry point.
  * @retval int
  */
int main(void)
{

  /* MCU Configuration--------------------------------------------------------*/

  /* Reset of all peripherals, Initializes the Flash interface and the Systick. */
  HAL_Init();

  /* Configure the system clock */
  SystemClock_Config();

  /* Initialize all configured peripherals */
  MX_GPIO_Init();
  MX_TIM1_Init();
  MX_FDCAN1_Init();
  MX_ADC1_Init();
  MX_SPI1_Init();
  MX_USART1_UART_Init();
  MX_CORDIC_Init();
  /* USER CODE BEGIN 2 */

  static uint8_t data_tx[4] = {0x0F, 0x00, 0x04, 0x07};
  static uint8_t data_rx[4];


  HAL_GPIO_WritePin(HALL_SPI_CS_GPIO_Port, HALL_SPI_CS_Pin, GPIO_PIN_RESET);
  HAL_SPI_TransmitReceive(&hspi1, data_tx, data_rx, 4, 500);
  HAL_GPIO_WritePin(HALL_SPI_CS_GPIO_Port, HALL_SPI_CS_Pin, GPIO_PIN_SET);

  HAL_Delay(1);

  // reg 0
  data_tx[0] = 0x00;
  data_tx[1] = 0x51;
  data_tx[2] = 0x20;
  data_tx[3] = 0x00;

  HAL_GPIO_WritePin(HALL_SPI_CS_GPIO_Port, HALL_SPI_CS_Pin, GPIO_PIN_RESET);
  HAL_SPI_TransmitReceive(&hspi1, data_tx, data_rx, 4, 500);
  HAL_GPIO_WritePin(HALL_SPI_CS_GPIO_Port, HALL_SPI_CS_Pin, GPIO_PIN_SET);

  // reg 1
  data_tx[0] = 0x01;
  data_tx[1] = 0x01;
  data_tx[2] = 0xd5;
  data_tx[3] = 0x00;

  HAL_GPIO_WritePin(HALL_SPI_CS_GPIO_Port, HALL_SPI_CS_Pin, GPIO_PIN_RESET);
  HAL_SPI_TransmitReceive(&hspi1, data_tx, data_rx, 4, 500);
  HAL_GPIO_WritePin(HALL_SPI_CS_GPIO_Port, HALL_SPI_CS_Pin, GPIO_PIN_SET);

  // 300mt, x32 oversampling


  // zrobic odczyt i transmisja uatrtemz osi x, y , z z porasto konwersja klub bez

  int16_t x, y, z;
  float fx, fy, fz;
  char buffer[50];
  int len;

  /* USER CODE END 2 */

  /* Infinite loop */
  /* USER CODE BEGIN WHILE */
  while (1)
  {
	  data_tx[0] = 0x89;
	  data_tx[1] = 0x00;
	  data_tx[2] = 0x00;
	  data_tx[3] = 0x00;

	  HAL_GPIO_WritePin(HALL_SPI_CS_GPIO_Port, HALL_SPI_CS_Pin, GPIO_PIN_RESET);
	  HAL_SPI_TransmitReceive(&hspi1, data_tx, data_rx, 4, 100);
	  HAL_GPIO_WritePin(HALL_SPI_CS_GPIO_Port, HALL_SPI_CS_Pin, GPIO_PIN_SET);

	  x = ((data_rx[1] << 8U) & 0xFF00) | data_rx[2];

	  data_tx[0] = 0x8a;
	  data_tx[1] = 0x00;
	  data_tx[2] = 0x00;
	  data_tx[3] = 0x00;

	  HAL_GPIO_WritePin(HALL_SPI_CS_GPIO_Port, HALL_SPI_CS_Pin, GPIO_PIN_RESET);
	  HAL_SPI_TransmitReceive(&hspi1, data_tx, data_rx, 4, 100);
	  HAL_GPIO_WritePin(HALL_SPI_CS_GPIO_Port, HALL_SPI_CS_Pin, GPIO_PIN_SET);

	  y = ((data_rx[1] << 8U) & 0xFF00) | data_rx[2];

	  data_tx[0] = 0x8b;
	  data_tx[1] = 0x00;
	  data_tx[2] = 0x00;
	  data_tx[3] = 0x00;

	  HAL_GPIO_WritePin(HALL_SPI_CS_GPIO_Port, HALL_SPI_CS_Pin, GPIO_PIN_RESET);
	  HAL_SPI_TransmitReceive(&hspi1, data_tx, data_rx, 4, 100);
	  HAL_GPIO_WritePin(HALL_SPI_CS_GPIO_Port, HALL_SPI_CS_Pin, GPIO_PIN_SET);

	  z = ((data_rx[1] << 8U) & 0xFF00) | data_rx[2];

	  fx = ConvertRawToMilliTesla(x);
	  fy = ConvertRawToMilliTesla(y);
	  fz = ConvertRawToMilliTesla(z);

//      len = snprintf(buffer, sizeof(buffer), "%u  %u  %u\r\n", (uint16_t)x, (uint16_t)y, (uint16_t)z);
//	  HAL_UART_Transmit(&huart1, (uint8_t*)buffer, len, HAL_MAX_DELAY);

      len = snprintf(buffer, sizeof(buffer), "%.1f  %.1f  %.1f\r\n", fx, fy, fz);
	  HAL_UART_Transmit(&huart1, (uint8_t*)buffer, len, HAL_MAX_DELAY);

	  HAL_Delay(300);

    /* USER CODE END WHILE */

    /* USER CODE BEGIN 3 */
  }
  /* USER CODE END 3 */
}

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


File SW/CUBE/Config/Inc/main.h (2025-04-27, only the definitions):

#define DEBUG_PIN_RED_Pin GPIO_PIN_13
#define DEBUG_PIN_RED_GPIO_Port GPIOC
#define DEBUG_PIN_BLUE_Pin GPIO_PIN_15
#define DEBUG_PIN_BLUE_GPIO_Port GPIOC
#define NRST_Pin GPIO_PIN_10
#define NRST_GPIO_Port GPIOG
#define MOTOR_DRV_SOC_Pin GPIO_PIN_1
#define MOTOR_DRV_SOC_GPIO_Port GPIOC
#define MOTOR_DRV_SOB_Pin GPIO_PIN_2
#define MOTOR_DRV_SOB_GPIO_Port GPIOC
#define MOTOR_DRV_SOA_Pin GPIO_PIN_3
#define MOTOR_DRV_SOA_GPIO_Port GPIOC
#define BEMF_C_Pin GPIO_PIN_0
#define BEMF_C_GPIO_Port GPIOA
#define BEMF_B_Pin GPIO_PIN_1
#define BEMF_B_GPIO_Port GPIOA
#define BEMF_A_Pin GPIO_PIN_2
#define BEMF_A_GPIO_Port GPIOA
#define HALL_SPI_CS_Pin GPIO_PIN_4
#define HALL_SPI_CS_GPIO_Port GPIOA
#define HALL_SPI_SCK_Pin GPIO_PIN_5
#define HALL_SPI_SCK_GPIO_Port GPIOA
#define HALL_SPI_MISO_Pin GPIO_PIN_6
#define HALL_SPI_MISO_GPIO_Port GPIOA
#define HALL_SPI_MOSI_Pin GPIO_PIN_7
#define HALL_SPI_MOSI_GPIO_Port GPIOA
#define HALL_ALERT_Pin GPIO_PIN_4
#define HALL_ALERT_GPIO_Port GPIOC
#define USER_LED_Pin GPIO_PIN_0
#define USER_LED_GPIO_Port GPIOB
#define USER_BUTTON_Pin GPIO_PIN_1
#define USER_BUTTON_GPIO_Port GPIOB
#define VBAT_SENSE_Pin GPIO_PIN_11
#define VBAT_SENSE_GPIO_Port GPIOB
#define MOTOR_DRV_INLA_Pin GPIO_PIN_13
#define MOTOR_DRV_INLA_GPIO_Port GPIOB
#define MOTOR_DRV_INLB_Pin GPIO_PIN_14
#define MOTOR_DRV_INLB_GPIO_Port GPIOB
#define MOTOR_DRV_INLC_Pin GPIO_PIN_15
#define MOTOR_DRV_INLC_GPIO_Port GPIOB
#define MOTOR_DRV_NFAULT_Pin GPIO_PIN_7
#define MOTOR_DRV_NFAULT_GPIO_Port GPIOC
#define MOTOR_DRV_NSLEEP_Pin GPIO_PIN_8
#define MOTOR_DRV_NSLEEP_GPIO_Port GPIOC
#define MOTOR_DRV_INHA_Pin GPIO_PIN_8
#define MOTOR_DRV_INHA_GPIO_Port GPIOA
#define MOTOR_DRV_INHB_Pin GPIO_PIN_9
#define MOTOR_DRV_INHB_GPIO_Port GPIOA
#define MOTOR_DRV_INHC_Pin GPIO_PIN_10
#define MOTOR_DRV_INHC_GPIO_Port GPIOA
#define CAN_TRCV_STB_Pin GPIO_PIN_11
#define CAN_TRCV_STB_GPIO_Port GPIOC
#define UART_TX_Pin GPIO_PIN_6
#define UART_TX_GPIO_Port GPIOB
#define UART_RX_Pin GPIO_PIN_7
#define UART_RX_GPIO_Port GPIOB
#define BOOT_Pin GPIO_PIN_8
#define BOOT_GPIO_Port GPIOB

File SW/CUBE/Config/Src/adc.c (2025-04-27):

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
/* Includes ------------------------------------------------------------------*/
#include "adc.h"

ADC_HandleTypeDef hadc1;

/* ADC1 init function */
void MX_ADC1_Init(void)
{

  ADC_MultiModeTypeDef multimode = {0};
  ADC_ChannelConfTypeDef sConfig = {0};

  /** Common config
  */
  hadc1.Instance = ADC1;
  hadc1.Init.ClockPrescaler = ADC_CLOCK_SYNC_PCLK_DIV4;
  hadc1.Init.Resolution = ADC_RESOLUTION_12B;
  hadc1.Init.DataAlign = ADC_DATAALIGN_RIGHT;
  hadc1.Init.GainCompensation = 0;
  hadc1.Init.ScanConvMode = ADC_SCAN_DISABLE;
  hadc1.Init.EOCSelection = ADC_EOC_SINGLE_CONV;
  hadc1.Init.LowPowerAutoWait = DISABLE;
  hadc1.Init.ContinuousConvMode = DISABLE;
  hadc1.Init.NbrOfConversion = 1;
  hadc1.Init.DiscontinuousConvMode = DISABLE;
  hadc1.Init.ExternalTrigConv = ADC_SOFTWARE_START;
  hadc1.Init.ExternalTrigConvEdge = ADC_EXTERNALTRIGCONVEDGE_NONE;
  hadc1.Init.DMAContinuousRequests = DISABLE;
  hadc1.Init.Overrun = ADC_OVR_DATA_PRESERVED;
  hadc1.Init.OversamplingMode = DISABLE;
  if (HAL_ADC_Init(&hadc1) != HAL_OK)
  {
    Error_Handler();
  }

  /** Configure the ADC multi-mode
  */
  multimode.Mode = ADC_MODE_INDEPENDENT;
  if (HAL_ADCEx_MultiModeConfigChannel(&hadc1, &multimode) != HAL_OK)
  {
    Error_Handler();
  }

  /** Configure Regular Channel
  */
  sConfig.Channel = ADC_CHANNEL_7;
  sConfig.Rank = ADC_REGULAR_RANK_1;
  sConfig.SamplingTime = ADC_SAMPLETIME_2CYCLES_5;
  sConfig.SingleDiff = ADC_SINGLE_ENDED;
  sConfig.OffsetNumber = ADC_OFFSET_NONE;
  sConfig.Offset = 0;
  if (HAL_ADC_ConfigChannel(&hadc1, &sConfig) != HAL_OK)
  {
    Error_Handler();
  }
}

void HAL_ADC_MspInit(ADC_HandleTypeDef* adcHandle)
{

  GPIO_InitTypeDef GPIO_InitStruct = {0};
  RCC_PeriphCLKInitTypeDef PeriphClkInit = {0};
  if(adcHandle->Instance==ADC1)
  {
  /** Initializes the peripherals clocks
  */
    PeriphClkInit.PeriphClockSelection = RCC_PERIPHCLK_ADC12;
    PeriphClkInit.Adc12ClockSelection = RCC_ADC12CLKSOURCE_SYSCLK;
    if (HAL_RCCEx_PeriphCLKConfig(&PeriphClkInit) != HAL_OK)
    {
      Error_Handler();
    }

    /* ADC1 clock enable */
    __HAL_RCC_ADC12_CLK_ENABLE();

    __HAL_RCC_GPIOC_CLK_ENABLE();
    __HAL_RCC_GPIOA_CLK_ENABLE();
    __HAL_RCC_GPIOB_CLK_ENABLE();
    /**ADC1 GPIO Configuration
    PC1     ------> ADC1_IN7
    PC2     ------> ADC1_IN8
    PC3     ------> ADC1_IN9
    PA0     ------> ADC1_IN1
    PA1     ------> ADC1_IN2
    PA2     ------> ADC1_IN3
    PB11     ------> ADC1_IN14
    */
    GPIO_InitStruct.Pin = MOTOR_DRV_SOC_Pin|MOTOR_DRV_SOB_Pin|MOTOR_DRV_SOA_Pin;
    GPIO_InitStruct.Mode = GPIO_MODE_ANALOG;
    GPIO_InitStruct.Pull = GPIO_NOPULL;
    HAL_GPIO_Init(GPIOC, &GPIO_InitStruct);

    GPIO_InitStruct.Pin = BEMF_C_Pin|BEMF_B_Pin|BEMF_A_Pin;
    GPIO_InitStruct.Mode = GPIO_MODE_ANALOG;
    GPIO_InitStruct.Pull = GPIO_NOPULL;
    HAL_GPIO_Init(GPIOA, &GPIO_InitStruct);

    GPIO_InitStruct.Pin = VBAT_SENSE_Pin;
    GPIO_InitStruct.Mode = GPIO_MODE_ANALOG;
    GPIO_InitStruct.Pull = GPIO_NOPULL;
    HAL_GPIO_Init(VBAT_SENSE_GPIO_Port, &GPIO_InitStruct);

  }
}

void HAL_ADC_MspDeInit(ADC_HandleTypeDef* adcHandle)
{

  if(adcHandle->Instance==ADC1)
  {
    /* Peripheral clock disable */
    __HAL_RCC_ADC12_CLK_DISABLE();

    /**ADC1 GPIO Configuration
    PC1     ------> ADC1_IN7
    PC2     ------> ADC1_IN8
    PC3     ------> ADC1_IN9
    PA0     ------> ADC1_IN1
    PA1     ------> ADC1_IN2
    PA2     ------> ADC1_IN3
    PB11     ------> ADC1_IN14
    */
    HAL_GPIO_DeInit(GPIOC, MOTOR_DRV_SOC_Pin|MOTOR_DRV_SOB_Pin|MOTOR_DRV_SOA_Pin);

    HAL_GPIO_DeInit(GPIOA, BEMF_C_Pin|BEMF_B_Pin|BEMF_A_Pin);

    HAL_GPIO_DeInit(VBAT_SENSE_GPIO_Port, VBAT_SENSE_Pin);

  }
}



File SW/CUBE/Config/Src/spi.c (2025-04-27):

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
/* Includes ------------------------------------------------------------------*/
#include "spi.h"

SPI_HandleTypeDef hspi1;

/* SPI1 init function */
void MX_SPI1_Init(void)
{

  hspi1.Instance = SPI1;
  hspi1.Init.Mode = SPI_MODE_MASTER;
  hspi1.Init.Direction = SPI_DIRECTION_2LINES;
  hspi1.Init.DataSize = SPI_DATASIZE_8BIT;
  hspi1.Init.CLKPolarity = SPI_POLARITY_LOW;
  hspi1.Init.CLKPhase = SPI_PHASE_1EDGE;
  hspi1.Init.NSS = SPI_NSS_SOFT;
  hspi1.Init.BaudRatePrescaler = SPI_BAUDRATEPRESCALER_16;
  hspi1.Init.FirstBit = SPI_FIRSTBIT_MSB;
  hspi1.Init.TIMode = SPI_TIMODE_DISABLE;
  hspi1.Init.CRCCalculation = SPI_CRCCALCULATION_DISABLE;
  hspi1.Init.CRCPolynomial = 7;
  hspi1.Init.CRCLength = SPI_CRC_LENGTH_DATASIZE;
  hspi1.Init.NSSPMode = SPI_NSS_PULSE_ENABLE;
  if (HAL_SPI_Init(&hspi1) != HAL_OK)
  {
    Error_Handler();
  }
}

void HAL_SPI_MspInit(SPI_HandleTypeDef* spiHandle)
{

  GPIO_InitTypeDef GPIO_InitStruct = {0};
  if(spiHandle->Instance==SPI1)
  {
    /* SPI1 clock enable */
    __HAL_RCC_SPI1_CLK_ENABLE();

    __HAL_RCC_GPIOA_CLK_ENABLE();
    /**SPI1 GPIO Configuration
    PA5     ------> SPI1_SCK
    PA6     ------> SPI1_MISO
    PA7     ------> SPI1_MOSI
    */
    GPIO_InitStruct.Pin = HALL_SPI_SCK_Pin|HALL_SPI_MISO_Pin|HALL_SPI_MOSI_Pin;
    GPIO_InitStruct.Mode = GPIO_MODE_AF_PP;
    GPIO_InitStruct.Pull = GPIO_NOPULL;
    GPIO_InitStruct.Speed = GPIO_SPEED_FREQ_LOW;
    GPIO_InitStruct.Alternate = GPIO_AF5_SPI1;
    HAL_GPIO_Init(GPIOA, &GPIO_InitStruct);

    /* SPI1 interrupt Init */
    HAL_NVIC_SetPriority(SPI1_IRQn, 0, 0);
    HAL_NVIC_EnableIRQ(SPI1_IRQn);
  }
}

void HAL_SPI_MspDeInit(SPI_HandleTypeDef* spiHandle)
{

  if(spiHandle->Instance==SPI1)
  {
    /* Peripheral clock disable */
    __HAL_RCC_SPI1_CLK_DISABLE();

    /**SPI1 GPIO Configuration
    PA5     ------> SPI1_SCK
    PA6     ------> SPI1_MISO
    PA7     ------> SPI1_MOSI
    */
    HAL_GPIO_DeInit(GPIOA, HALL_SPI_SCK_Pin|HALL_SPI_MISO_Pin|HALL_SPI_MOSI_Pin);

    /* SPI1 interrupt Deinit */
    HAL_NVIC_DisableIRQ(SPI1_IRQn);
  }
}



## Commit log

2025-03-31 pcb: Add BOM
    [bom.xlsx]
2025-04-02 pcb: Add electrical schematic
2025-04-13 pcb: Add layout & gerbers
    [FOC_Controller.kicad_pcb, FOC_Controller.kicad_sch, bom.xlsx]
2025-04-26 enclosure: Add enclosure STL files
    [Base.stl, Lid.stl, Lid_for_development.stl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]
2025-04-27 pcb: Update BOM
    [bom.xlsx]
2025-04-27 pcb: Add PCB step files
    [FOC_Controller.step]
2025-04-27 cube: Add Stm32CubeIde project template
2025-04-27 cube: Create README.md for STM32CubeIde project template

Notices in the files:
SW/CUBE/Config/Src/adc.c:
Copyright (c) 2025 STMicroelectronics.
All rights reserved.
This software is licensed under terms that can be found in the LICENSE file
